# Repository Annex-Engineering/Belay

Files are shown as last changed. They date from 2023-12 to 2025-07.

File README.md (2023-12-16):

# Belay - Extruder Sync Sensor



Belay is a sensor for FFF 3D printers for keeping a secondary extruder
in sync with the primary extruder, avoiding error accumulation
regardless of how long a print may be. Either a
[Trad Rack](https://github.com/Annex-Engineering/TradRack) or a normal
extruder can be used as the secondary extruder. See
[purpose and how it works](#purpose-and-how-it-works) for more
details.

This project is inspired by the Filament Buffer used by Bambu Lab on their X1
and P1 Series printers.

Our discord server can be found here: 

Join me on Discord (https://discord.gg/MzTR3zE)

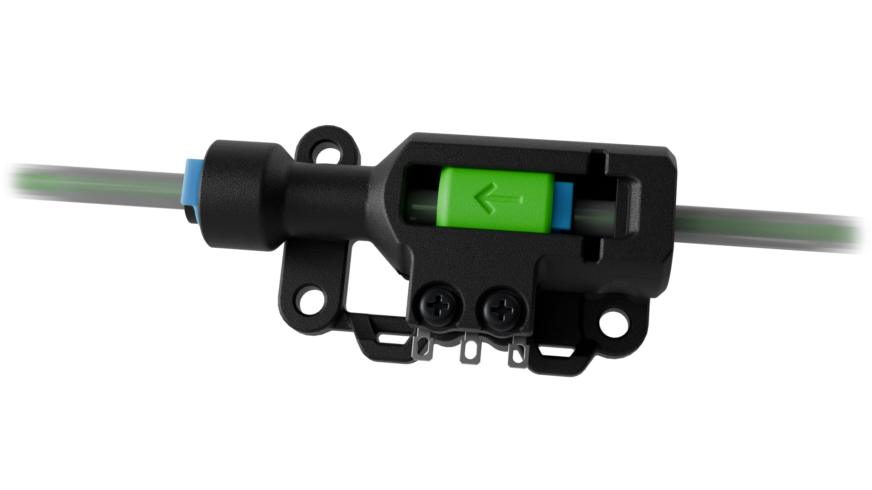
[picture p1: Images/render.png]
Image of Belay


## Getting started

See the [Quick Start document](/docs/Quick_Start.md) to get started.

## Purpose and how it works

Long filament paths or very heavy spools can cause extra resistance
in filament movement, potentially causing the printer's extruder to
struggle. One solution is to add a secondary extruder in series with
the primary extruder to take some of the load; often the secondary
extruder is synced directly to the primary extruder.

However, without a feedback system, the 2 extruders may gradually
drift out of sync from even a small mismatch in how well their
`rotation_distance` calibrations match the actual movement ratios.
Longer prints will build up to a larger mismatch, which may add extra
resistance to the filament's movement and eventually cause one of the
extruders to slip or skip.

Belay prevents error accumulation by dynamically adjusting the
`rotation_distance` setting of the secondary extruder to prevent
buildup of excess slack or tension in the filament between the 2
extruders. The bowden tube going from the secondary extruder to the
primary extruder is split into 2 pieces, and Belay goes between them.
When extruding forward, if the tubes before and after Belay
start getting pulled together, it sets a higher multiplier (lower
`rotation_distance`) for the secondary extruder. If the tubes start
getting pushed apart, it sets a lower multiplier. The multipliers are
reversed when extruding backward.

The following gif shows Belay in use during a print with exaggerated
multipliers of 1.30 and 0.70 to illustrate its movement:

Belay Demo

(With the default multipliers of 1.05 and 0.95, the movement of the
slider is much slower and shorter and becomes difficult to see, at
least without very high extrusion flowrates)

## Status and future plans

Belay is currently in open alpha. The code has been in use by a few
people using Trad Rack and has been working well so far, but the
current mechanical design is relatively new and may change
significantly.

Some things we may want to try in the future:

- Using an analog hall effect sensor (or similar) and PID control,
  instead of the digital switch and bang-bang control that is
  currently used
- Using the sensor to detect clogs/tangles (for example by detecting
  if the slider reaches either end of its travel via a 2nd switch or by
  replacing the digital switch with an analog one, using an analog
  sensor to determine if the slider is moving too fast for the
  commanded extrusion speed, etc.)

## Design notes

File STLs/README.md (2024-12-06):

# What to print

All parts in the STLs folder need to be printed, with the exception
that some parts have multiple variants (for different bowden tube
collet types) and you only need 1 variant of each of these parts:

## Collet types

The following bowden tube collet types are supported:

- "5mm collet" (E3D V6, Bondtech LGX)
- "6mm collet" (UM2)
- ECAS04

The filename of each variant of the slider and sensor_housing STLs will contain
either `(5mm_collet)`, `(6mm_collet)`, or `(ecas04)` to indicate the collet type
it is meant for.

"5mm" and "6mm" refer to the approximate diameter of the part of the collet that
the collet clip goes around, highlighted in blue below:

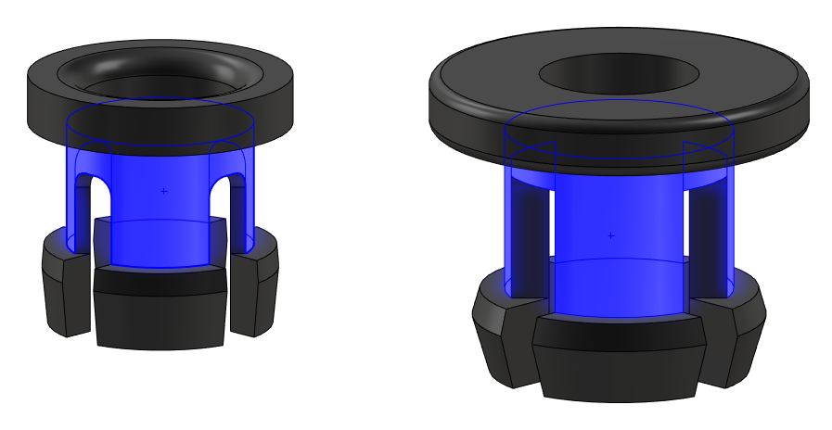
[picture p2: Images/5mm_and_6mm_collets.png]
5mm and 6mm collets


If using the 5mm or 6mm collet options, a collet clip should be used to prevent
the bowden tube from moving. A collet clip is unnecessary if using the ECAS04
option.

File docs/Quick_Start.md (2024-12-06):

# Quick Start

This document provides an overview of how to get a Belay sensor
running.

**Table of Contents**
- [Prerequisites](#prerequisites)
- [BOM/sourcing](#bomsourcing)
- [Printed parts](#printed-parts)
- [Assembly](#assembly)
- [Wiring](#wiring)
- [Kalico installation](#kalico-installation)
  - [Klippy module](#klippy-module)
    - [Klippy module installation](#klippy-module-installation)
    - [Enabling Moonraker updates](#enabling-moonraker-updates)
  - [Config files](#config-files)
- [Testing](#testing)
  - [Check sensor polarity](#check-sensor-polarity)
  - [First print](#first-print)
- [Further reading](#further-reading)

## Prerequisites

Your 3D printer must meet the following requirements to work with
Belay:

- Must use 1.75mm filament.
- Must run [Kalico](http://github.com/KalicoCrew/kalico) or
  [Klipper](https://github.com/Klipper3d/klipper) firmware.
- The toolhead or primary extruder must have a collet/coupling to
  secure a 4mm bowden tube at its inlet. The secondary extruder must
  have one at its outlet as well.

## BOM/sourcing

The following hardware is required:

| Component/Item | Qty Required  | Notes |
| --- | --- | --- |
| Omron D2F-L Microswitch | 1 | See Trad Rack BOM/sourcing guide for other variants that will work  |
| Collet | 2 | See Trad Rack BOM/sourcing guide for an ECAS04 source |
| Collet clip | 2 | Only needed if using a 5mm or 6mm collet |
| M2 x 12mm Pan Head Self Tapping Screw | 2 | Longer screws will also work but will stick out |

See [the STLs README](/STLs/README.md#collet-types) for collet type options.
Some example sources for 5mm/6mm collets and collet clips:
- 5mm collet - [KB3D](https://kb-3d.com/store/spare-parts/487-bondtech-push-fit-collar-for-bowden-coupling-175mm-7350011413331.html)
- 5mm collet clip - [KB3D](https://kb-3d.com/store/e3d/48-e3d-bowden-collet-clip-175mm-1644688775189.html)
- 6mm collet and collet clip - [AliExpress](https://www.aliexpress.us/item/2255801046836641.html)

See the
[Annex BOM/sourcing guide](https://docs.google.com/spreadsheets/d/1O3eyVuQ6M4F03MJSDs4Z71_XyNjXL5HFTZr1jsaAtRc/edit?usp=sharing)
for recommended sources for all other components.

## Printed parts

See the following files/folders:

- [Print Settings and File Key](/Print_Settings_and_File_Key.txt):
  print settings to use and info on reading the STL filenames.
- [STLs folder](/STLs): contains all STL files.
- [STLs README](/STLs/README.md): information on what parts to print.

## Assembly

This section lists the assembly steps. If you are using ECAS04 collets, you can
ignore any time a step tells you to add a collet clip.

Insert the 2 collets into the sensor housing and slider:

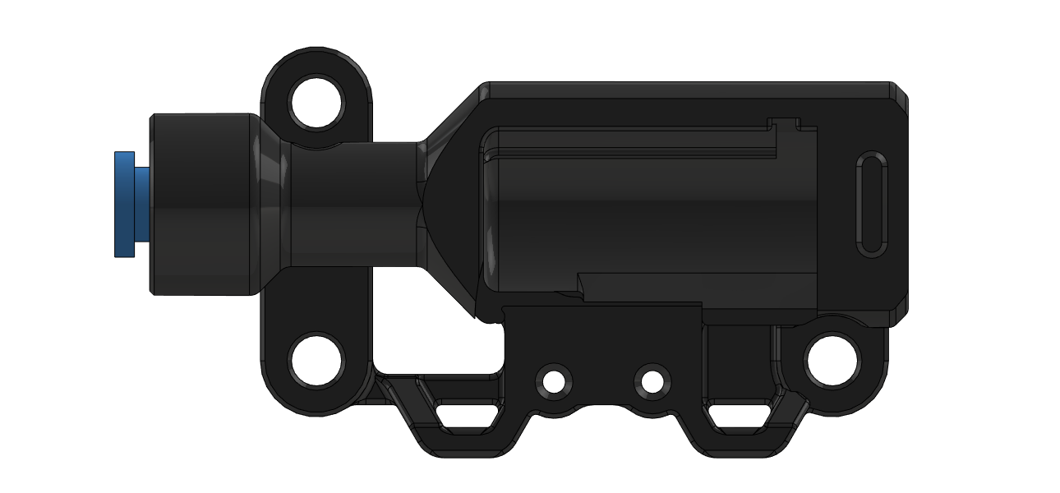
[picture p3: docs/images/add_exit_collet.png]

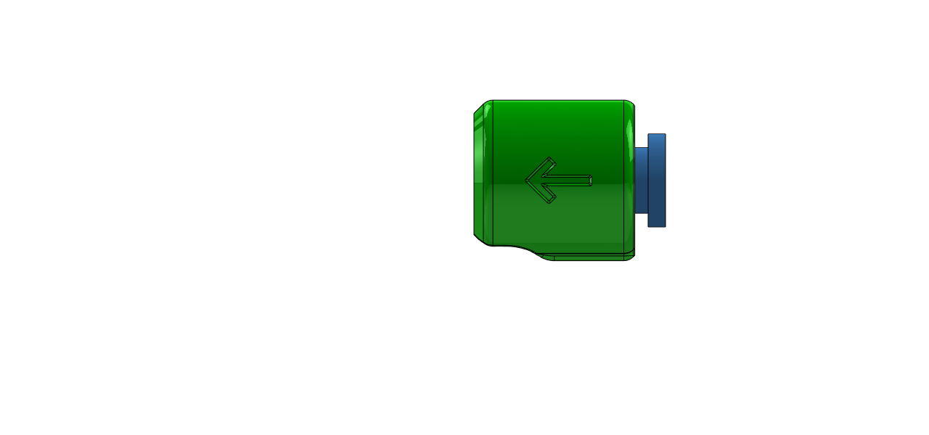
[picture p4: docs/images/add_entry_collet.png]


Place the slider into the sensor housing. Make sure the arrow is visible and
facing the same direction as in the image:

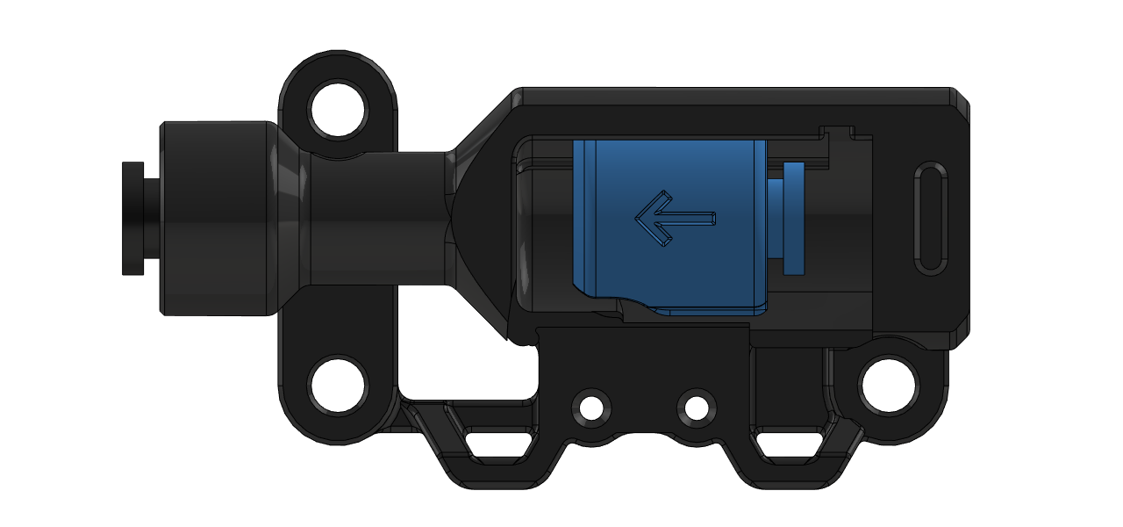
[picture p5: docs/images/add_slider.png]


Place the cover onto the sensor housing:

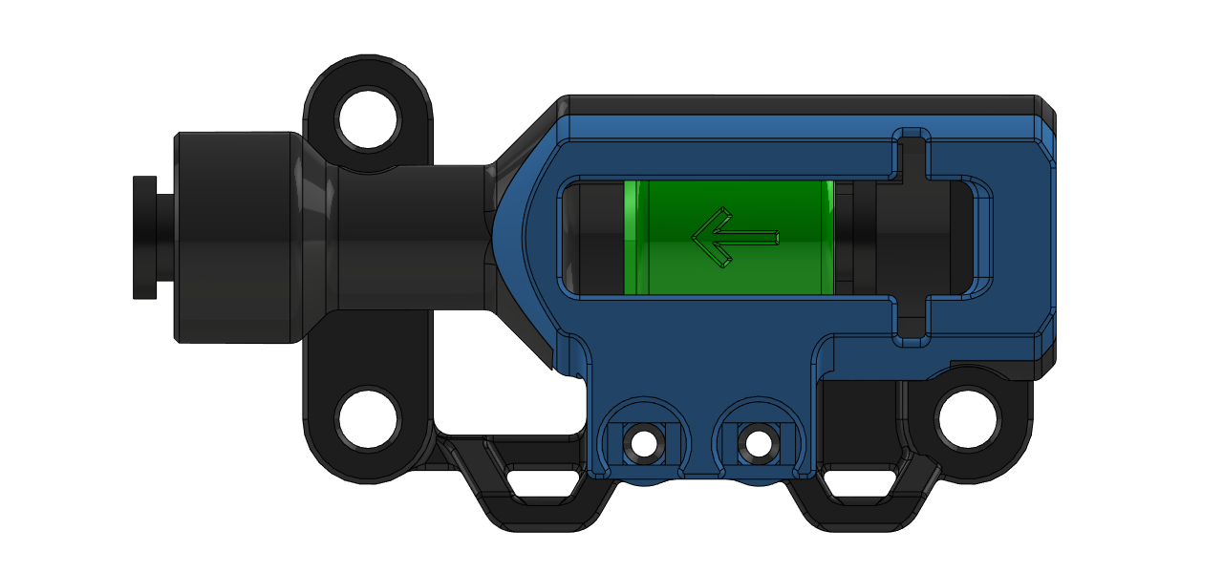
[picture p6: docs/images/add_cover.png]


Insert the microswitch from the bottom and secure with 2 M2x12 screws (going
through the cover, through the switch, and into the sensor housing). Make sure
the tip of the lever on the microswitch is pointing to the left:

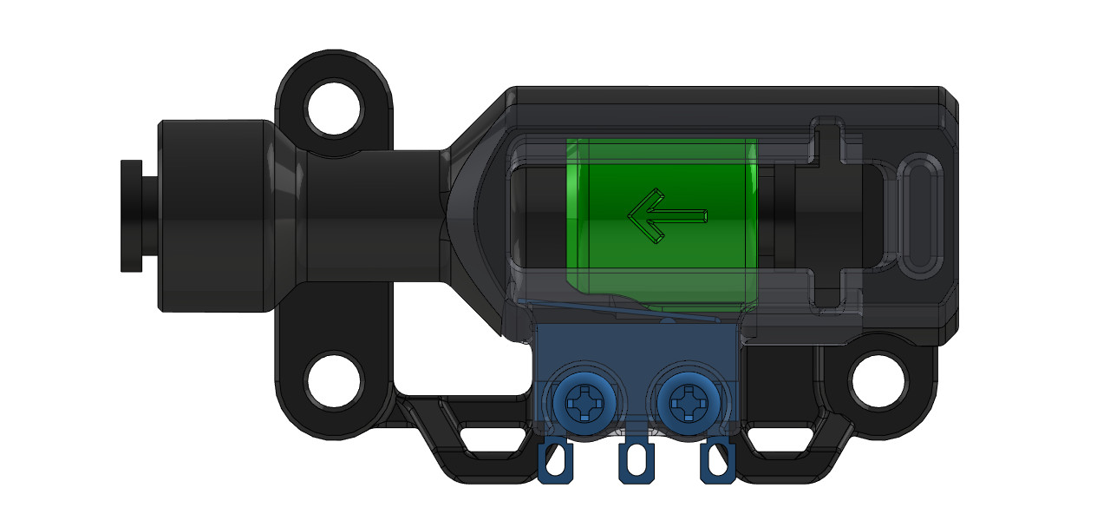
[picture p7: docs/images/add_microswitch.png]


Push the slider to the left until it reaches the end of its travel.
Then insert the entry bowden tube and push it in as far as it can go.
The tube should extend past the left end of the slider and into the
sensor housing:

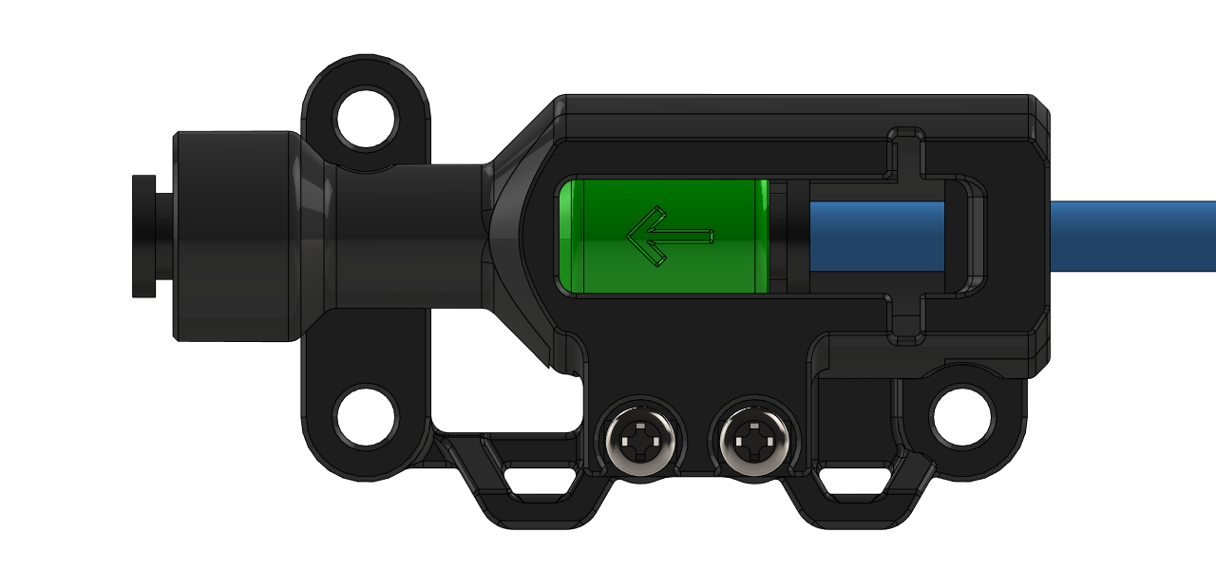
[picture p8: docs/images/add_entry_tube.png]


Gently pull the tube until the slider reaches the other end of its travel:

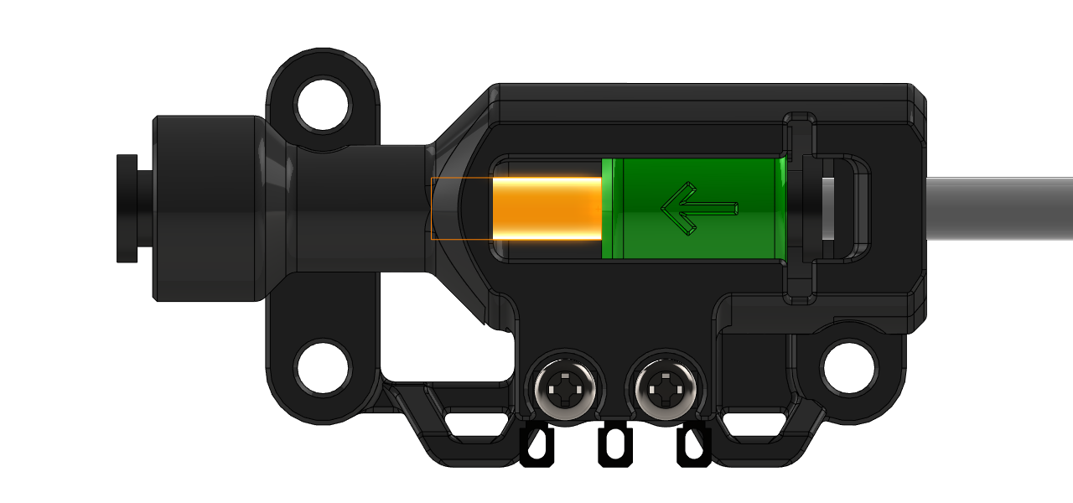
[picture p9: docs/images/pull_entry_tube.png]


> [!IMPORTANT]
> The tube should extend past the left end of the slider and into the sensor
> housing, as shown by the orange highlighted portion in the image above. If you
> can see a gap in the filament path, then the tube was not inserted all the
> way, and you need to retry the previous 2 steps (move the slider to the left
> end of its travel before pushing the tube further in, then pull the tube until
> the slider reaches the right end of its travel).

Add a collet clip by inserting it through the slot in the cover:

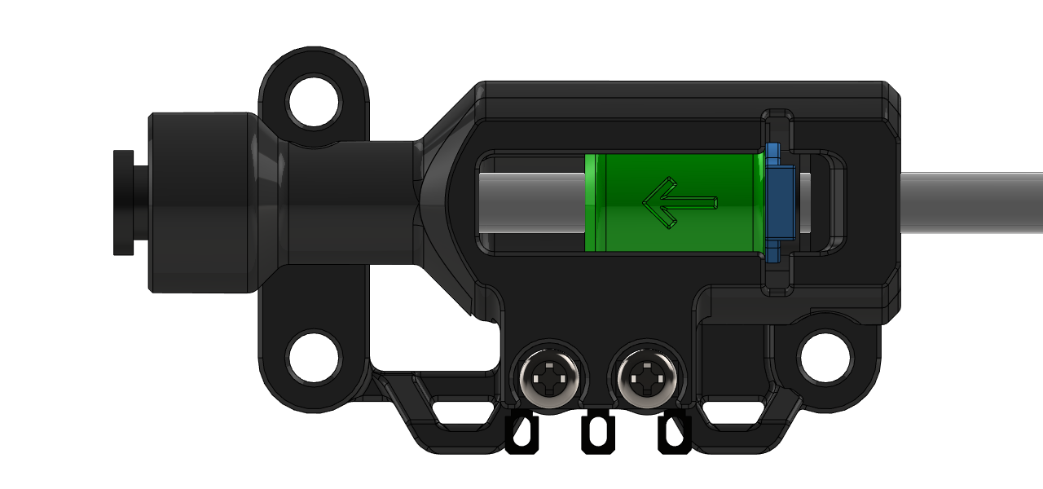
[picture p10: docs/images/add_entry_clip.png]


Insert the exit bowden tube, then add a collet clip:

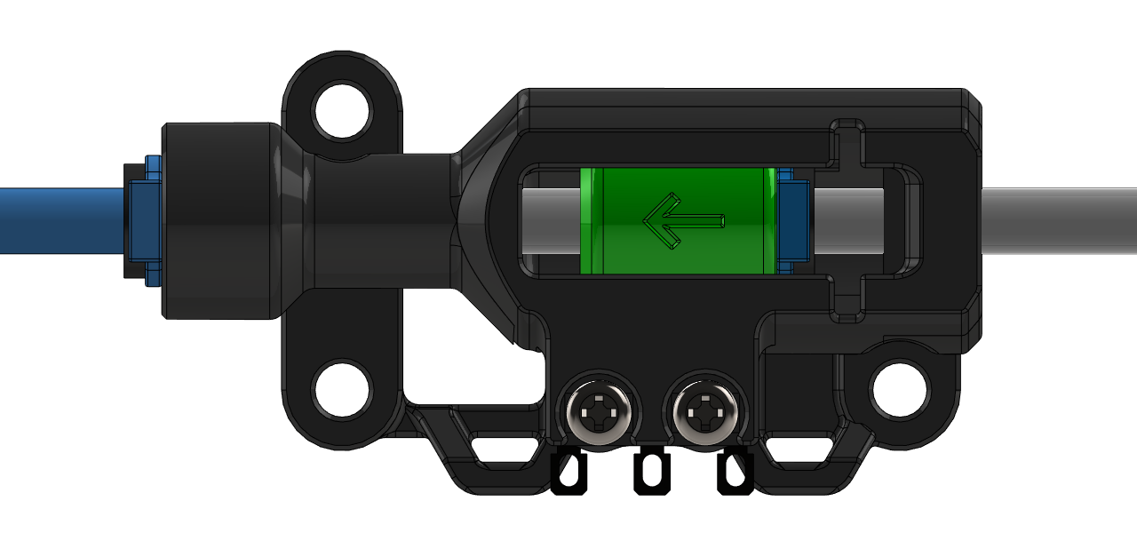
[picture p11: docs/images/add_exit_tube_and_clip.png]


## Wiring

The microswitch has 3 solder points, but we're only going to be using 2 of them. Specifically, we'll be using the two solder points on the left and right sides of the housing. You can ignore the middle one.

The wires will not be used to carry any substantial current. So you don't have to worry about using a specific gauge of wire.

Solder 2 wires to the microswitch as shown below:

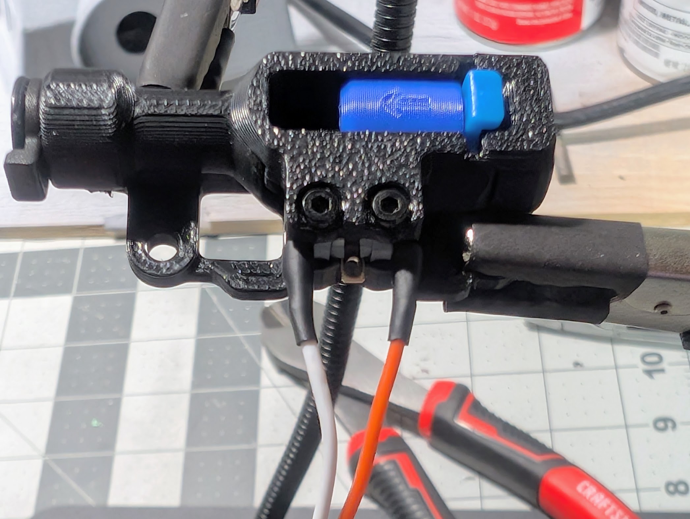
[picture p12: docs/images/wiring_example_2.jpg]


Make sure you secure them to the sensor housing with a
zip tie as shown below. This will keep any stresses from moving the belay around off the solder points.

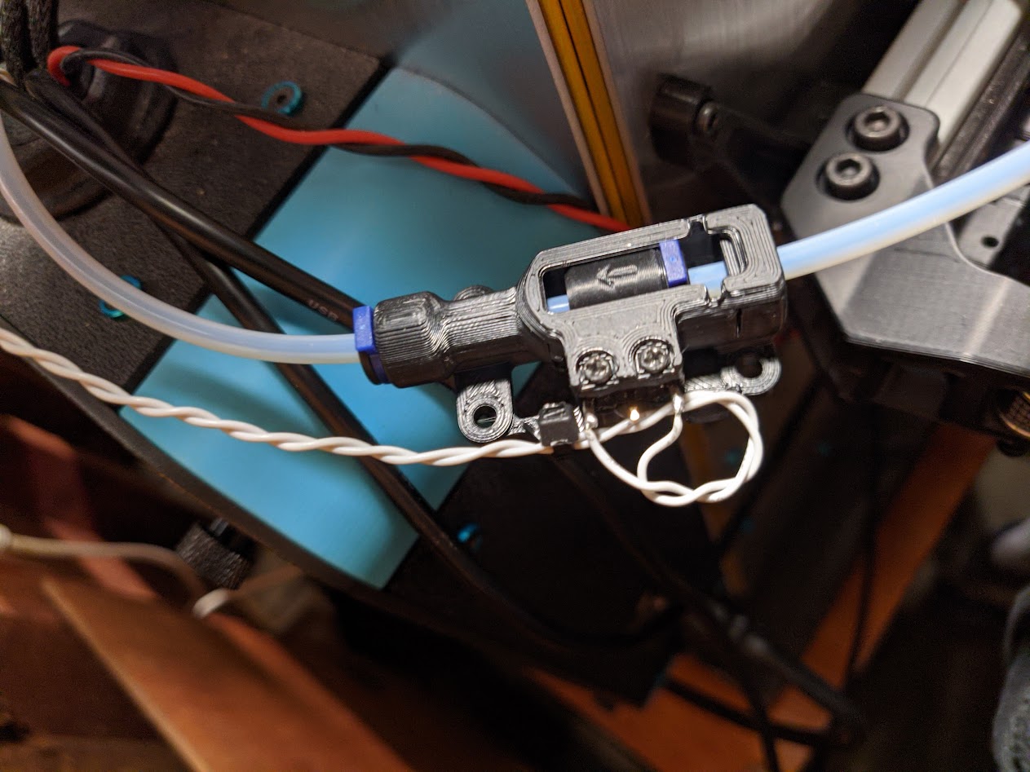
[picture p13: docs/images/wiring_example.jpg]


Next, you'll need to identify a port on your controller board to use. An endstop port is the easiest option, but you can use almost any available port with an input signal pin and a ground pin. Make sure you note the microcontroller pin name for the signal pin of this port, as you'll need it when we get to setting up the belay in Kalico or Klipper later. In this example, we'll be using an endstop port. This is a 3-pin port, and connects using a JST-XH connector.

The port's pins are 3.3v, ground, and signal. The Belay only needs to connect to the ground and signal pins. You'll need to crimp the wires and then make sure you insert them in the connector aligned with the proper pins. It does not matter which wire is connected to ground or signal.
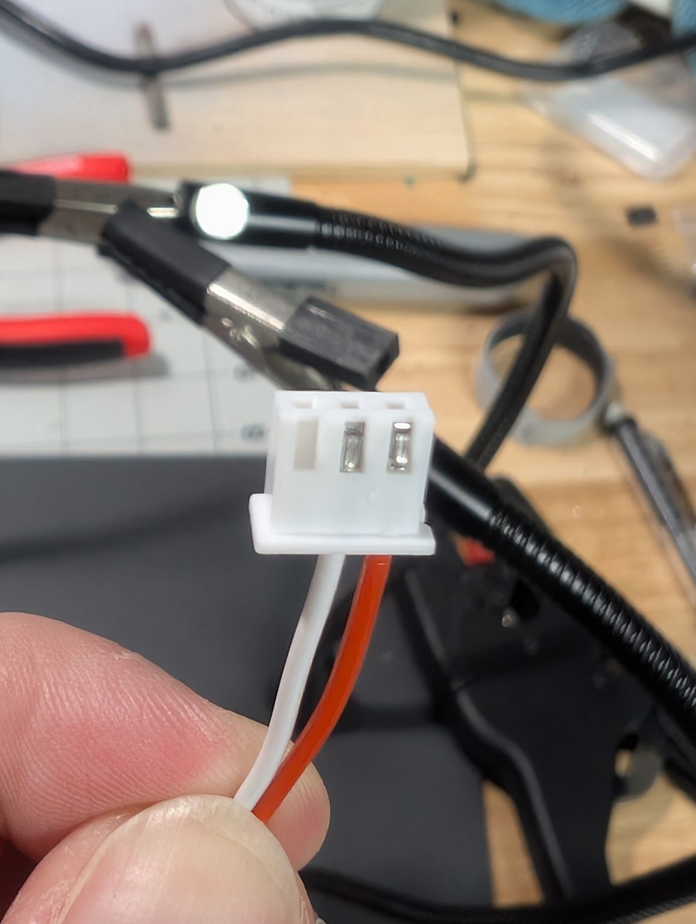
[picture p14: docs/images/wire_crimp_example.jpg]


That's all it takes to wire the belay. Whenever you're ready, you can run the wire and plug it in to your printer's controller board. Remember that sensor pin name for the next steps.

## Kalico installation

This section lists the steps to get Belay set up to work with Kalico or Klipper:

### Klippy module

This section involves adding the Belay Klippy module(s) to Klipper
and enabling updates through Moonraker.

If you are using [Kalico](http://github.com/KalicoCrew/kalico),
you can skip to [setting up config files](#config-files) since
Kalico already includes the belay module.

#### Klippy module installation

Run the following commands to download and install the Klippy
module(s):

```
cd ~
curl -LJO https://raw.githubusercontent.com/Annex-Engineering/Belay/main/Kalico/klippy_module/install.sh
chmod +x install.sh
./install.sh
```

Then remove the install script with the following command:

```
rm install.sh
```

Finally, restart the klipper service using the following command:

```
sudo systemctl restart klipper
```

> [!TIP]
> If you ever need to run the install script again in the future (for
> example if additional Klippy modules get added), you can do so
> without recreating the `belay_klippy_module` directory using the
> following commands:
> ```
> cd ~
> ./belay_klippy_module/Kalico/klippy_module/install.sh <branch_name>
> ```
> If unspecified, `branch_name` defaults to `main`.

#### Enabling Moonraker updates

To enable updates of the Belay Klippy module(s) through Moonraker,
add the following to your `moonraker.conf` file. This file is usually
located in `~/printer_data/config/`:

```
[update_manager belay]
type: git_repo
path: ~/belay_klippy_module
origin: https://github.com/Annex-Engineering/Belay.git
primary_branch: main
managed_services: klipper
```

Then restart the moonraker service using the following command:

```
sudo systemctl restart moonraker
```

### Config files

Sample config files are provided for different secondary extruder
types. Copy the file from the corresponding subfolder of the
[kalico_config folder](/Kalico/kalico_config/) and
[include it](https://docs.kalico.gg/Config_Reference.html#include)
in your main printer config file.

Change the `sensor_pin` config option to match the pin you are using.
In addition, make sure to follow all instructions left in the comments
of the config file (which are specific to the type of secondary
extruder you are using) for any further changes that may be needed.

Restart Kalico once you have finished making changes to the config
file(s).

## Testing

This section explains how to test that Belay is working properly:

### Check sensor polarity

Push the bowden tubes before and after Belay together by hand so that
Belay is compressed. Run the following command and observe the console
output:

```
QUERY_BELAY BELAY=my_belay
```

Then pull the bowden tubes apart so that Belay is expanded and run
the command again.

The expected result is that the console should have reported that
belay my_belay was "compressed" the first time and "expanded" the
second time. If these are reversed, add or remove `!` in the value for
`sensor_pin` in the config file. If the reported states matched, then
it is likely that either the wrong pin was used or there is a problem
with wiring.

### First print

During a print, Belay's slider should stay close to the middle of its
travel range without hitting either end.

The recommended starting value for the `debug_level` config option is
`1`. With this setting, the extruder multiplier set by Belay will be
reported in the console whenever Belay's switch changes state.

Throughout a print with `debug_level` set to 1, the reported
multiplier should generally flip back and forth between the values of
the config options `multiplier_high` and `multiplier_low` (which
default to `1.05` and `0.95` respectively). However, it is possible
that the same multiplier may appear in the console 2 or more times in
a row if the state of the switch changed during a retraction; this is
normal.

If Belay seems to be working and you do not want to see these messages
in the console anymore, you can set `debug_level` to `0` in the config
to disable them.

## Further reading

See the [Overview document](README.md) to see the full documents
available for Belay, for example to see all available gcode commands
or config options.

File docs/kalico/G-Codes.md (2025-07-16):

# G-Codes

This document is modeled after Kalico's
[G-Codes document](https://docs.kalico.gg/G-Codes.html) but only
contains items pertaining to Belay.

### QUERY_BELAY
`QUERY_BELAY BELAY=<config_name>`: Queries the state of the belay
specified by `BELAY`.

### BELAY_SET_MULTIPLIER
`BELAY_SET_MULTIPLIER BELAY=<config_name> [HIGH=<multiplier_high>]
[LOW=<multiplier_low>]`: Sets the values of multiplier_high and/or
multiplier_low for the belay specified by `BELAY`, overriding their
values from the corresponding
[belay config section](Config_Reference.md#belay). Values set by this
command will not persist across restarts.

### ENABLE_BELAY
`ENABLE_BELAY BELAY=<config_name>`: Enables extrusion multiplier adjustments by
the belay specified by `BELAY` for its corresponding secondary extruder.

### DISABLE_BELAY
`DISABLE_BELAY BELAY=<config_name> [OVERRIDE=<0|1>]`: Resets the extrusion
multiplier for the secondary extruder corresponding to the belay specified by
`BELAY` and disables extrusion multiplier adjustments by the belay. If
`OVERRIDE` is 1, then the specified belay cannot be re-enabled automatically
until the ENABLE_BELAY or BELAY_CLEAR_OVERRIDE command is used with the same
belay specified for the `BELAY` parameter. The `OVERRIDE` parameter currently is
only relevant if extruder_type is set to 'trad_rack' in the corresponding
[belay config section](Config_Reference.md#belay). If not specified,
`OVERRIDE` defaults to 0.

### BELAY_CLEAR_OVERRIDE
`BELAY_CLEAR_OVERRIDE BELAY=<config_name>`: Clears any override set by the
DISABLE_BELAY command that would prevent the belay specified by `BELAY` from
being automatically enabled.

### BELAY_SET_STEPPER
`BELAY_SET_STEPPER BELAY=<config_name> STEPPER=<extruder_stepper_name>`: Selects
the extruder_stepper whose multiplier will be controlled by the belay specified
by `BELAY`. The multiplier for the previous stepper will be reset back
to 1 before switching to the new stepper. Stepper selections made by this
command will not persist across restarts. This command is only available if
extruder_type is set to 'extruder_stepper' in the corresponding
[belay config section](Config_Reference.md#belay).

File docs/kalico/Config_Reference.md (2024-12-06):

# Belay Configuration reference

This document is modeled after Kalico's
[Config Reference document](https://docs.kalico.gg/Config_Reference.html)
but only contains items pertaining to Belay.

### [belay]

Belay extruder sync sensors (one may define any number of sections
with a "belay" prefix).

```
[belay my_belay]
extruder_type:
#   The type of secondary extruder. Available choices are 'trad_rack'
#   or 'extruder_stepper'. This parameter must be specified.
extruder_stepper_name:
#   The name of the extruder_stepper being used as the secondary
#   extruder. Must be specified if extruder_type is set to
#   'extruder_stepper', but should not be specified otherwise. For
#   example, if the config section for the secondary extruder is
#   [extruder_stepper my_extruder_stepper], this parameter's value
#   would be 'my_extruder_stepper'.
#multiplier_high: 1.05
#   High multiplier to set for the secondary extruder when extruding
#   forward and Belay is compressed or when extruding backward and
#   Belay is expanded. The default is 1.05.
#multiplier_low: 0.95
#   Low multiplier to set for the secondary extruder when extruding
#   forward and Belay is expanded or when extruding backward and
#   Belay is compressed. The default is 0.95.
#debug_level: 0
#   Controls messages sent to the console. If set to 0, no messages
#   will be sent. If set to 1, multiplier resets will be reported, and
#   the multiplier will be reported whenever it is set in response to
#   a switch state change. If set to 2, the behavior is the same as 1
#   but with an additional message whenever the multiplier is set in
#   response to detecting an extrusion direction change. The default
#   is 0.
```

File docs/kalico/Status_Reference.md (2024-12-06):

# Status Reference

This document is modeled after Kalico's
[Status Reference document](https://docs.kalico.gg/Status_Reference.html)
but only contains items pertaining to Belay.

## belay

The following information is available in
[belay some_name](Config_Reference.md#belay) objects:
- `printer["belay <config_name>"].last_state`: Returns True if the belay's
  sensor is in a triggered state (indicating its slider is compressed).
- `printer["belay <config_name>"].enabled`: Returns True if the belay is
  currently enabled.

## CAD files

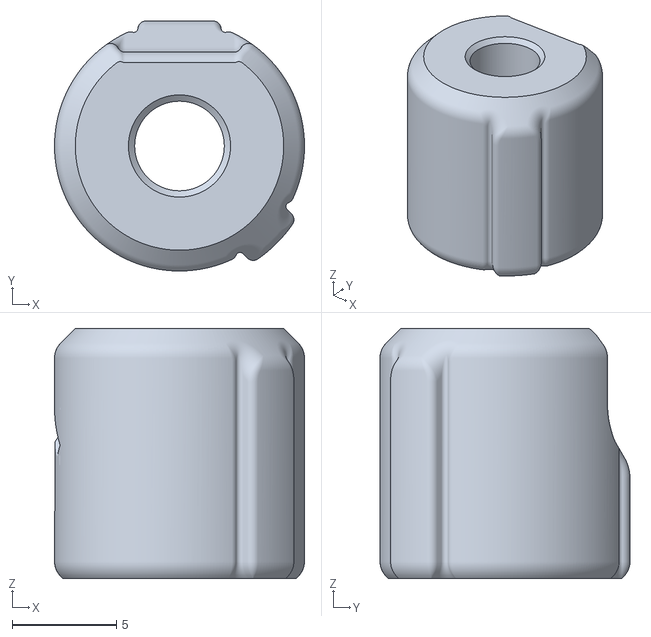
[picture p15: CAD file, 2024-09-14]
STLs/[a]_slider_(ecas04)_x1_rev1.STL
12.0 x 12.0 x 12.0

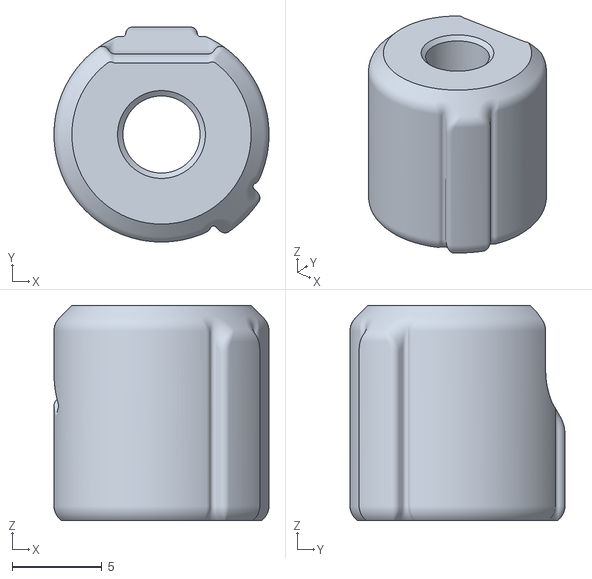
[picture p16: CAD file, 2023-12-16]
STLs/[a]_slider_(5mm_collet)_x1_rev2.STL
12.0 x 12.0 x 12.0

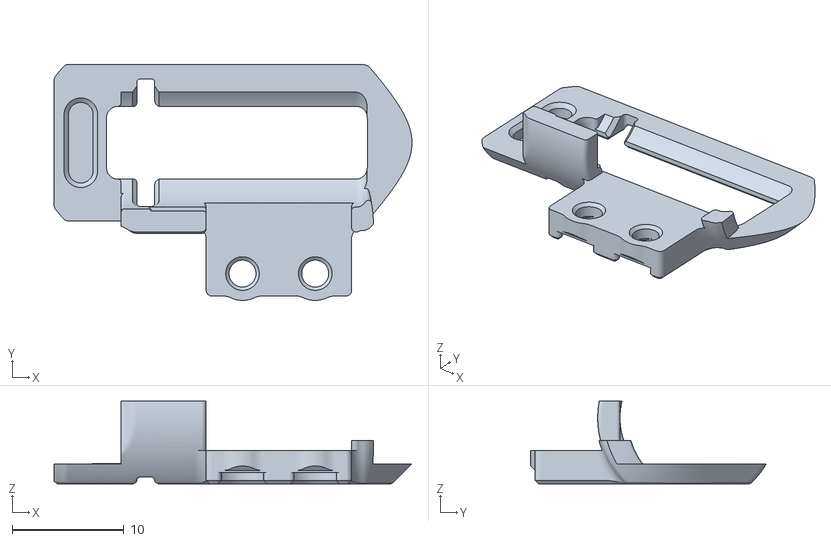
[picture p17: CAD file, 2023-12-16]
STLs/cover_x1_rev2.STL
32.0 x 21.1 x 7.40

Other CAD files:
STLs/[a]_slider_(6mm_collet)_x1_rev2.STL

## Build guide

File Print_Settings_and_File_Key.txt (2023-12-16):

Primary Color: nothing at start of file name
Accent Color: [a]_ at start of file name
Quantity Required: _x# near end of file name
File Revision: _rev# at end of file name

Do not use XY compensation, hole shrinking compensation, or any
similar slicer setting that modifies the geometry to try to account
for shrinkage. Elephant foot compensation (also known as XY first
layer compensation) is okay.

Nozzle Size: 0.5mm 
Recommended FDM Materials: ASA, Polymaker or 3DXTech Recommended
Alternate Approved FDM Materials: PC, 3DXTech Recommended
Layer Height: 0.20mm to 0.25mm
Extrusion Width: Forced 0.5mm
Infill Percentage: 40% minimum (at 0.8mm Width)
Infill Type: Grid, Gyroid, Honeycomb, Triangle or Cubic
Wall Count: 3 minimum (at 0.5mm Width)
Solid Top/Bottom Layers: 4 minimum (at 0.5mm Height)

Nozzle Size: 0.4mm 
Recommended FDM Materials: ASA, Polymaker or 3DXTech Recommended
Alternate Approved FDM Materials: PC, 3DXTech Recommended
Layer Height: 0.20mm to 0.25mm
Extrusion Width: 0.40 to 0.45mm
Infill Percentage: 40% minimum (at 0.6mm Width)
Infill Type: Grid, Gyroid, Honeycomb, Triangle or Cubic
Wall Count: 4 minimum (at 0.4mm Width)
Solid Top/Bottom Layers: 4 minimum (at 0.25mm Height)

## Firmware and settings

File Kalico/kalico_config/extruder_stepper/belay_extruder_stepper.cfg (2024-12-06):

[belay my_belay]
extruder_type: extruder_stepper
extruder_stepper_name: my_extruder_stepper
sensor_pin: ^PA0
multiplier_high: 1.05
multiplier_low: 0.95
debug_level: 1

[extruder_stepper my_extruder_stepper]
extruder: extruder
#step_pin:
#dir_pin:
#enable_pin:
#microsteps:
#rotation_distance:
#   The above commented-out parameters must be set. These should match
#   what you would use in the [extruder] section if you used this
#   extruder as your primary extruder. Other parameters such as
#   full_steps_per_rotation or gear_ratio may also be useful or
#   needed.
#   
#   See the "stepper" section in Kalico's Configuration Reference for
#   details on these parameters:
#   https://docs.kalico.gg/Config_Reference.html#stepper
#
#   In addition, you may want to add a
#   [tmc2209 extruder_stepper my_extruder_stepper] section or similar:
#   https://docs.kalico.gg/TMC_Drivers.html

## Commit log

2023-10-27 Add support for an extruder-syncing sensor
2023-10-27 - Store just rotation distance instead of tuple - Fix case where the filament driver is not synced but the extruder sync sensor still tries to disable itself
2023-10-28 Ensure filament driver is synced before enabling extruder sync sensor
2023-11-19 - Support syncing during reverse extrusion - Simplify enable and disable events and ensure consistent behavior whether tip shaping comes from the gcode file or pre_unload_gcode - Replace verbose opti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
2023-12-14 - Rename to Belay - Add support for extruder_stepper as a secondary extruder option - Add ability to have multiple Belay sensors - Add gcode commands
2023-12-16 Add STLs, eDrawing, example config files, docs, etc.
    [belay_extruder_stepper.cfg, belay_trad_rack.cfg, cover_x1_rev2.STL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]
2024-01-27 Allow switching the extruder_stepper controlled by a belay
2024-04-07 Mention that Danger Klipper users can skip the module installation since the belay module is now included in Danger Klipper
2024-08-26 Add wiring instructions to the quick start guide
2024-09-14 Add ECAS04 option
    [slider_(ecas04)_x1_rev1.STL]
2024-10-05 Add reminder to check that the tube was inserted all the way
2024-10-05 Add accent color indicator
    [[a]_slider_(5mm_collet)_x1_rev2.STL, [a]_slider_(6mm_collet)_x1_rev2.STL, [a]_slider_(ecas04)_x1_rev1.STL]
2024-10-05 Add CAD
2024-12-06 Rename folders
    [belay_extruder_stepper.cfg, belay_trad_rack.cfg]
2024-12-06 Update docs for Kalico migration
    [belay_extruder_stepper.cfg]
2024-12-06 Add back Klipper_Stuff folder for now
2024-12-06 Add notice about the Klipper_Stuff folder no longer being used
2025-07-03 Estimate extruder direction based on future moves that will be affected instead of past ones
2025-07-03 Make changes from b1a653e compatible with versions of Klipper before Klipper3d/klipper@6cc409f
